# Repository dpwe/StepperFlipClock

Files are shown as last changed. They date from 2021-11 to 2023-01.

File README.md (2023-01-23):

# StepperFlipClock
2021-11-23

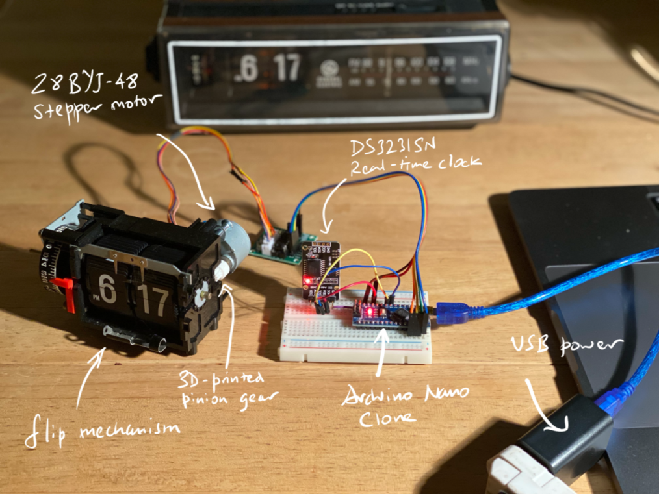
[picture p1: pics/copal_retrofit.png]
Copal retrofit components


Design and firmware for a stepper motor retrofit to the often-failed AC synchronous flip clock motors.

Flip clocks, perhaps most iconic from the repeating opening sequence of the movie Groundhog Day, are delightful mechanisms for rendering the time as digits by flipping through a set of leaves on a rotating drum like a rolodex.

They were popular as a "modern" clock in the 1960s and 70s, based on part on high-performance, mass-produced mechanisms from the Copal corporation in Japan, which manufactured high-quality flip mechanisms integrated with AC-synchronous motors, able to keep very accurate time thanks to the provision of extremely stable 50/60 Hz AC power by electrical utilities in many parts of the world.

Flip clocks were supplanted by the even more modern 7 segment LED clocks, and quartz time references, in the 1970s and 80s, but they now have a retro appeal. Unfortunately, the synchronous AC motors, spinning valiantly 8 times a second for 50 years or more, have long exceeded their design life and are mostly no longer functional.  They are no longer manufactured and no significant replacement stock has turned up.

At the same time, cheap and precise stepper motors of similar size and shape *are* available.  However, these need an entirely different source of time reference, and indeed require a microcontroller to operate.

This repo provides the resources for my investigations into stepper motor retrofit replacements for the original Copal synchronous motors found in the flip clocks made by GE (and Copal) in the eary 1970s.  I include the electronics design, the firmware (as Arduino sketches), and some pictures of a couple of finished clock conversions.

# BurstClockSerial

This version of the firmware winds on the flip mechanism in "bursts", once per minute.  This makes sure the flaps fall within a fraction of a second of the actual minute change; a regular flip mechanism typically has a variation of +/- 10 sec or more for any particular minute due to mechanical variations in the flaps.

The code has settings for two variations of the Copal mechanism, one with 60 teeth per hour on the main wheel (as found in GE clock-radios such as the 7-4305), and one with 50 teeth per hour (as in the Copal 227 alarm clock).

# synchronizer_nano

This sketch can be run on the same Arduino Nano that is driving the clock, but allows you to synchronize the DS3231 RTC chip to a time reference from a GPS.  You do this once, setting both the time and trimming the DS3231 to the GPS 1 second period, then you can re-run the BurstClockSerial to drive the clock.  To sync to GPS, you have to connect the GPS 1PPS signal to D2, and the GPS NMEA output to D8.

# StepperClockCopal.fzz

This is the Fritzing source for the hardware setup for the stepper clock.  It's mainly the wiring diagram that I've tried to make legible, although the schematic should be correct also.  It shows which Arduino pins are connected to which pins on the DS3231 RTC board, on the ULN2003A stepper driver board, as well as other hardware including the frontlight LED, the piezo buzzer, and the alarm microswitch.

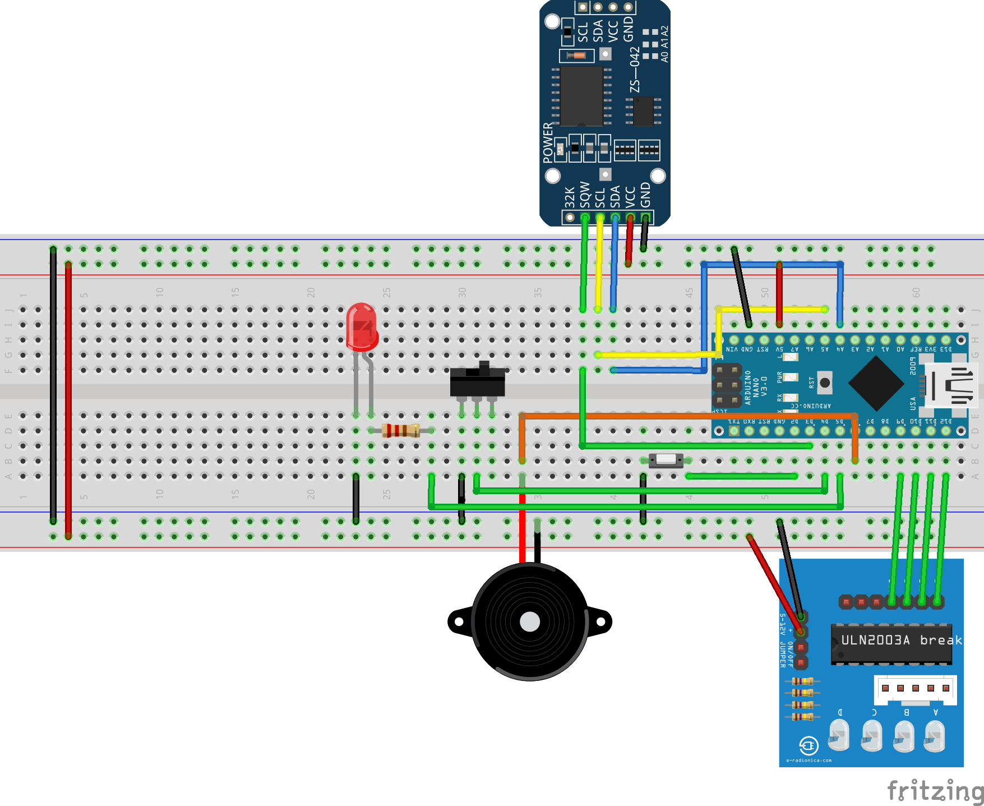
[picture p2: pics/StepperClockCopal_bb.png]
Stepper FlipClock Breadboard Layout


# 3Dprint

Directory containing the STL files I used for 3D printing pinion gears to mate the stepper motors with the flip clock mechanism.  `copol_pinion_1` works for the plastic-framed Copal mechanims.  `copol_pinion_2` attempted to scale down the teeth for the older, metal-framed mechanisms, but was a bit beyond the scale capabilities of the printing technology.  `copol_pinion_4b` converts the 5mm stepper shaft to the 2mm shaft on the original Copal motors, so you can take the small final gear off the early Copal motors and mount it on this 3D printed adapter.

# Gallery

In addition to the GE 7-4305 illustrated at the top of this page, I've also performed this retrofit on a Copal 227 which has much less space inside.  For this job, the power cord is replaced by a USB cord that plugs into an external USB power adapter at the mains plug.

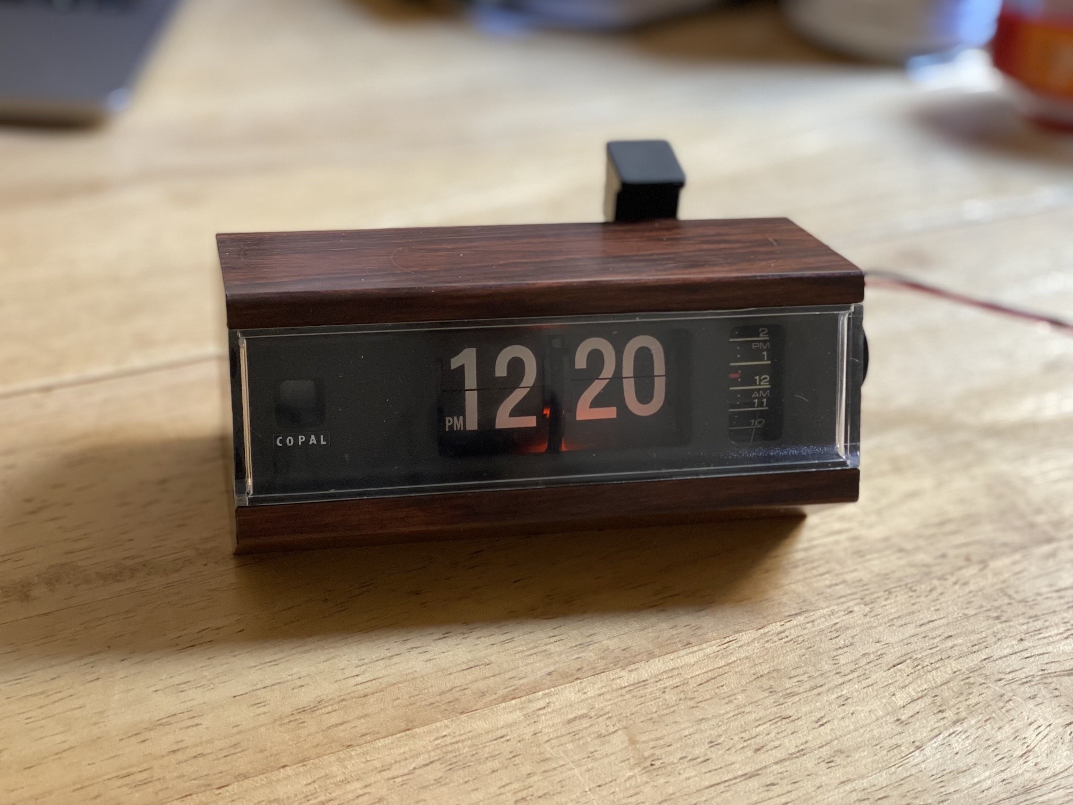
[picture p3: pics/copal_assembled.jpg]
Copal - assembled
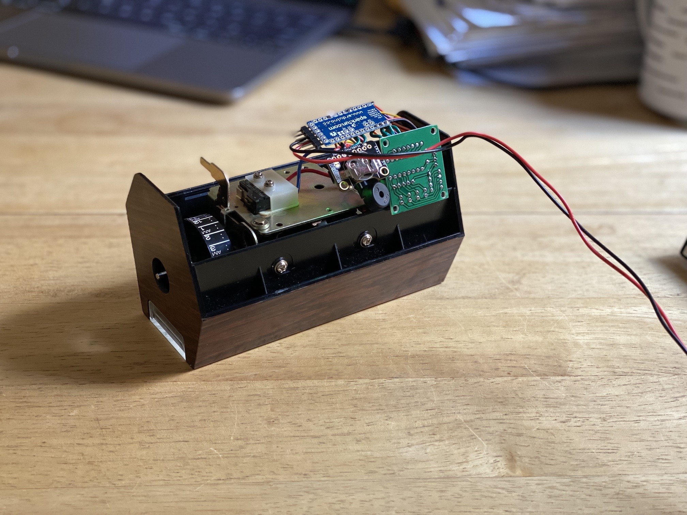
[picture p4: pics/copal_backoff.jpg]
Copal - back off
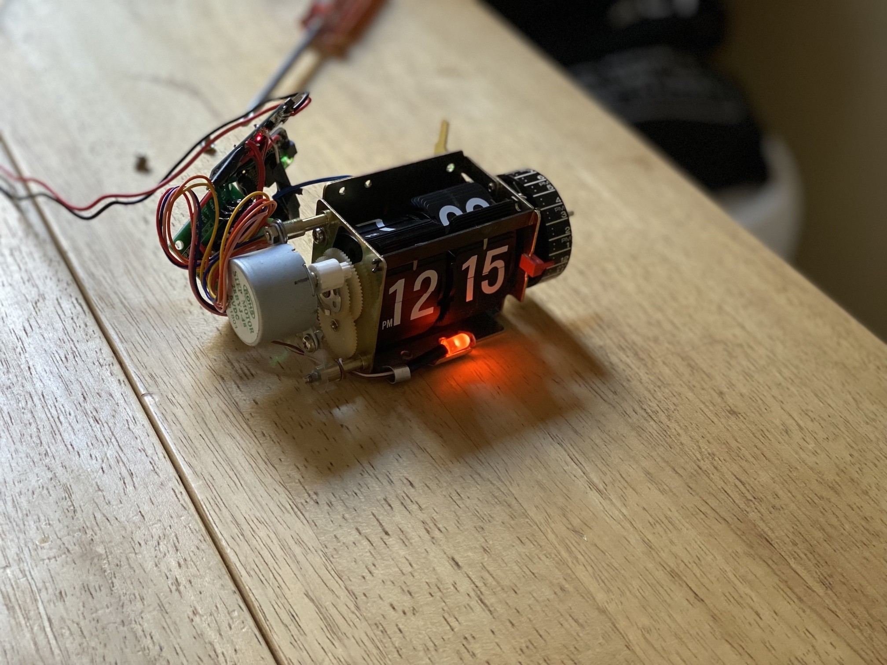
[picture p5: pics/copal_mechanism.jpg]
Copal - mechanism
  

# More Clock Adventures

See my [Clock Blog](https://dpwe.github.io/arduinoclocks/)

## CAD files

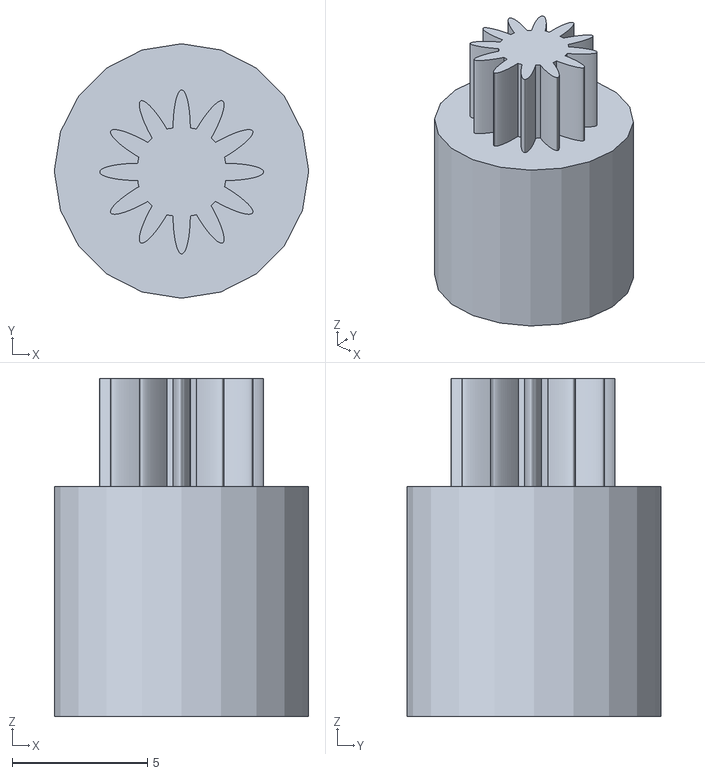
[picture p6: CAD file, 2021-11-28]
3Dprinting/copol_pinion_2.stl
9.40 x 9.40 x 12.5

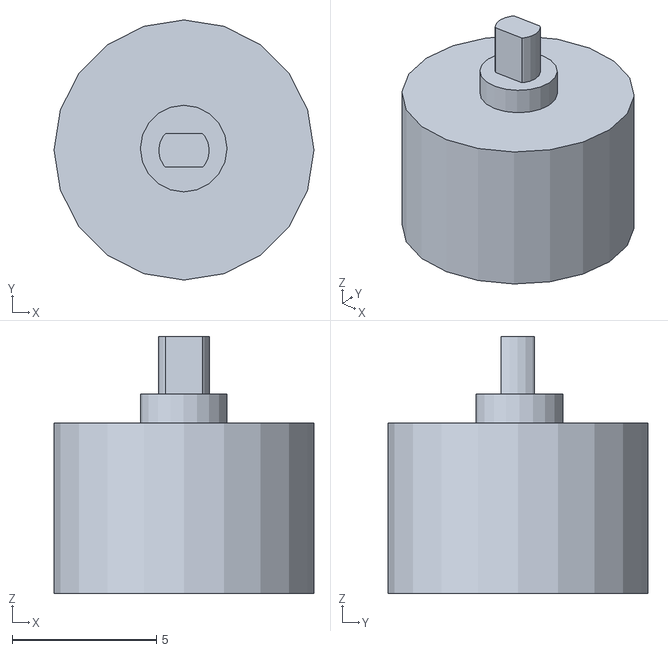
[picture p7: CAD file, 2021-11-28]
3Dprinting/copol_pinion_4b.stl
9.00 x 9.00 x 8.90

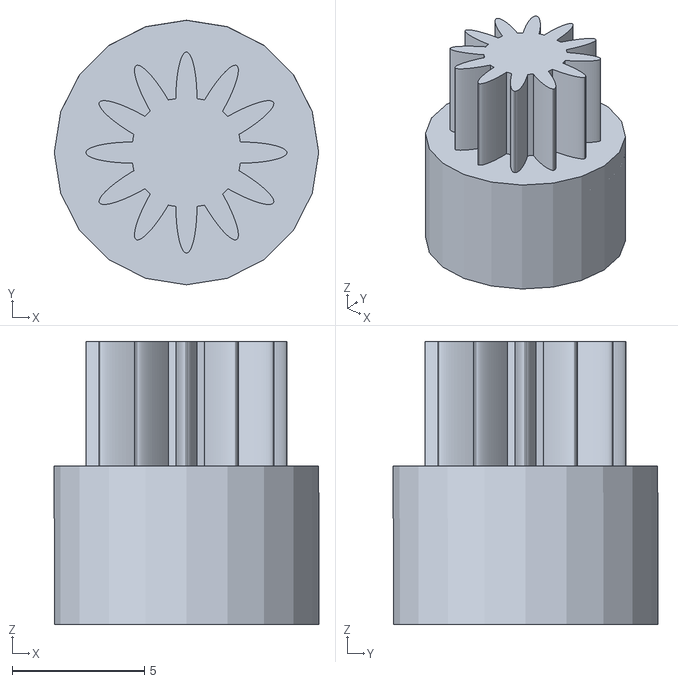
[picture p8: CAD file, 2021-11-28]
3Dprinting/copol_pinion_1.stl
10.0 x 10.0 x 10.7

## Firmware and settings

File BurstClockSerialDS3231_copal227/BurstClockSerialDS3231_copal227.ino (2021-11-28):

// BurstClockSerialDS3231.ino
// 
// Flip-clock-by-stepper-motor retrofit.
//
// Rather than emulating the continuous, slow rotation of the original Copal 60 Hz 
// synchronous motor, this version rotates by 1/12 rev as fast as possible once per
// minute.  This should allow us to control exactly when the flips fall, instead of 
// the +/- 15 sec of the original mechanism.  
//
// The code also aims to keep track of what the clock is currently displaying, and
// supports commanding to display arbitrary numbers.
//
// This version accepts control commands over the serial line.
// It uses the DS3231 instead of the MCP79412.  We use the DS3231's alarm register 
// as the battery-backed RAM to persist the current believed display state.

// Connections:
// ULN2003A board: (note, sequencing is backwards)
// IN1 -> D12
// IN2 -> D11
// IN3 -> D10
// IN4 -> D9
// DS3231 board:
// SDA -> A4
// SCL -> A5
// SQW -> D3 (supports interrupt)
// Clock Advance Button: -> D2 (pulls down to ground)
// Mechanical Alarm microswitch -> D4 (pulls down to ground when alarm should sound)
// Backlight LED -> D5 (supports Timer0 PWM, possibly interferes with delay() timer)
// Buzzer: Tone pattern on D6 (using Timer1, also D6 is OC0A, so might support PWM output)
// Time Wrong LED -> D13 (built-in LED)

// GE 7-4305
//#define STEPS_PER_CYCLE 2048
//#define MINUTES_PER_CYCLE 15
// Copal 227
#define STEPS_PER_CYCLE 1280
#define MINUTES_PER_CYCLE 9

#include <Tone.h>  // https://github.com/bhagman/Tone
Tone tone_out[2];  // Allocate two timers so we can *not* use tone_out[0],
                   // which tries to use Timer2 (but we have other plans).

#include <TimeLib.h>        // https://www.pjrc.com/teensy/td_libs_DS1307RTC.html
#include <Wire.h>           // https://www.arduino.cc/en/Reference/Wire

#include <Timezone.h>       // https://github.com/JChristensen/Timezone
// US Eastern Time Zone (New York, Detroit)
//TimeChangeRule myDST = {"EDT", Second, Sun, Mar, 2, -240};    //Daylight time = UTC - 4 hours
//TimeChangeRule mySTD = {"EST", First, Sun, Nov, 2, -300};     //Standard time = UTC - 5 hours
// US Pacific Time Zone (Las Vegas, Los Angeles)
TimeChangeRule myDST = {"PDT", Second, Sun, Mar, 2, -420};
TimeChangeRule mySTD = {"PST", First, Sun, Nov, 2, -480};
Timezone myTZ(myDST, mySTD);

#include <DS3231.h>         // https://github.com/NorthernWidget/DS3231
DS3231 ds3231;
RTClib RTC;

// -------------------------------------------------------------------
// Timer 2:
// Each time the stepper is advanced, Timer2 is set to generate an interrupt
// 3 ms later.  This interrupt either advances to the next step (if there are
// remaining steps to do) or powers down the coils.

// What to call on interrupt.
void (*_timeout_callback)(void);

// Timer2 Overflow Interrupt Vector
ISR(TIMER2_OVF_vect) {
  TIFR2 = 0x00;         // Timer2 INT Flag Reg: Clear Timer Overflow Interrupt
  TCCR2B = 0x00;        // Stop Timer2 until next timeout_restart().
  (*_timeout_callback)();
}

void timeout_setup(void (*callback_func)(void)) {
  // Set up Timer2 for the post-step timeout.
  TCCR2B = 0x00;        // Disable Timer2 while we set it up
  _timeout_callback = callback_func;
  TIFR2  = 0x00;        // Timer2 INT Flag Reg: Clear Timer Overflow Flag
  TIMSK2 = 0x01;        // Timer2 INT Reg: Timer2 Overflow Interrupt Enable
  TCCR2A = 0x00;        // Timer2 Control Reg A: Wave Gen Mode norm
}

void timeout_restart(unsigned int ms) {
  // Reset timeout timer (timer2). It counts up to 255 at 16 kHz, so 0 gives ~16ms, 128 is 8ms, 192 is 4ms.
  int init_val = 255 - (ms * 16);
  if (init_val < 0)  init_val = 0;  // max delay is 16 ms.
  TCNT2 = init_val;
  TCCR2B = 0x07;        // Timer2 Control Reg B: Timer Prescaler set to 1024 (starts the clock).
}

// -------------------------------------------------------------------
// Stepper motor control

// Pins to drive motor coils.
#define PIN_A 12
#define PIN_B 11
#define PIN_C 10
#define PIN_D 9

void stepper_setup(void)
{
  pinMode(PIN_A, OUTPUT);
  pinMode(PIN_B, OUTPUT);
  pinMode(PIN_C, OUTPUT);
  pinMode(PIN_D, OUTPUT);

  timeout_setup(next_step_callback);
}

void set_pins(int a, int b, int c, int d) {
  digitalWrite(PIN_A, a);
  digitalWrite(PIN_B, b);
  digitalWrite(PIN_C, c);
  digitalWrite(PIN_D, d);
}

void step_to_state(int state) {
  switch (state % 4) {
    // The "backwards" motion of the motor is encoded directly here.
    case 0:
      set_pins(0, 0, 1, 1);
      break;
    case 1:
      set_pins(0, 1, 1, 0);
      break;
    case 2:
      set_pins(1, 1, 0, 0);
      break;
    case 3:
      set_pins(1, 0, 0, 1);
      break;
  }
}

// Current steps within cycle of stepper
int _stepper_state = 0;
// We can peek at steps_to_do as a more informative alternative to stepper_active.
volatile long steps_to_do = 0;
// Semaphore that client writes to request more steps.  Gets cleared when accepted.
volatile long steps_to_do_semaphore = 0;
// Status that can be inspected by client.
volatile bool stepper_active = 0;

// When active, we advance the stepper every 3 ms.
#define MS_BETWEEN_STEPS 3

void next_step_callback(void)
{
  // This is usually executed in interrupt state, so be careful not to change variables used
  // outside, except the steps_to_do semaphore.
  if (steps_to_do_semaphore) {
    steps_to_do += steps_to_do_semaphore;
    steps_to_do_semaphore = 0;
  }
  if (steps_to_do) {
    stepper_active = 1;
    timeout_restart(MS_BETWEEN_STEPS);
    _stepper_state = (_stepper_state + 1) % STEPS_PER_CYCLE;
    step_to_state(_stepper_state);
    --steps_to_do;
  } else {
    // We are idling the stepper.
    stepper_active = 0;
    set_pins(0, 0, 0, 0);
    // Notify clients.
    //inc_display_minute();
    // Somehow this was being called during initialization and adding an extra minute.
    // Now inc_display_minute() is called by flip_update when it notices stepper_active 
    // has gone low.
  }
}

// Called by client to start new steps.
void add_steps(int steps) {
  // Drop the value into the semaphore; it will be added on to the total by the interrupt routine.
  Serial.print("add_steps=");
  Serial.println(steps);
  steps_to_do_semaphore = steps;
  if (!stepper_active) {
    // Calling next_step_callback will accept the semaphore, take a step immediately, then restart timer.
    next_step_callback();
  }
}

// ==========  persistent read/write =============

void save_display_state_to_sram(int mins_state) {
  // Write hrs/mins to DS3231 Alarm 2.  See DS3231.h
  byte disp_hour = (byte)(mins_state / 60);
  byte disp_min = (byte)(mins_state % 60);
  byte A2Day = 1, AlarmBits = 0;  // AlarmBits=0 means alarm when all of min, hr, day, month match.
  bool A2Dy = 0, A2h12 = 0, A2PM = 0;
  ds3231.setA2Time(A2Day, disp_hour, disp_min, AlarmBits, A2Dy, A2h12, A2PM);
}

int load_display_state_from_sram(void) {
  byte disp_hour, disp_min, A2Day, AlarmBits;
  bool A2Dy, A2h12, A2PM;
  ds3231.getA2Time(A2Day, disp_hour, disp_min, AlarmBits, A2Dy, A2h12, A2PM);
  if (A2h12 != 0) {
    Serial.println("DS3231 Alarm is in 12h mode - uh-oh!");
  }
  return 60 * (int)disp_hour + (int)disp_min;  
}

// -------------------------------------------------------------------
// Core flip-dispay driver.

// Keep track of where we are within the MINUTES_PER_CYCLE.
int current_minute = 0;
// Keep track of where we are within the STEPS_PER_CYCLE.
unsigned int current_step = 0;

#define MINS_PER_DAY 1440
// Believed current state of display, in minutes since midnight
// 0 = 00:00, 1439 = 23:59, -1 = unknown.
volatile int display_mins_shown = -1;

void inc_display_minute(void) {
  // Intended to be called by stepper interrupt routine when stepper goes idle because 
  // it has completed stepping.  However, it was being called "extra" during setup for 
  // an unexplained reason, so now it's called by the flip_update poll when it notices
  // a stepper command has finished.
  display_mins_shown = (display_mins_shown + 1) % MINS_PER_DAY;
}

void advance_one_minute(void) {
  ++current_minute;
  // Integer arithmetic - will round down.
  unsigned int new_step = (((long)current_minute * STEPS_PER_CYCLE) / MINUTES_PER_CYCLE);
  // Command the new steps to happen.
  add_steps(new_step - current_step);
  //Serial.print("steps: ");
  //Serial.println(new_step - current_step);
  // Update state.
  current_minute = current_minute % MINUTES_PER_CYCLE;
  current_step = new_step % STEPS_PER_CYCLE;
}

#define TIME_WRONG_LED LED_BUILTIN

void flip_setup(int initial_display_mins) {
  display_mins_shown = initial_display_mins;
  Serial.print("Setup ");
  flip_report_display(display_mins_shown);

  stepper_setup();
  // We use TIME_WRONG_LED to indicate when clock is "waiting" to catch up.
  pinMode(TIME_WRONG_LED, OUTPUT);
}

void set_time_error_led(bool state) {
  if (state) {
    digitalWrite(TIME_WRONG_LED, HIGH);
  } else {
    digitalWrite(TIME_WRONG_LED, LOW);    
  }
}

void printDigits(int digits)
{
  // utility function for digital clock display: prints preceding colon and leading 0
  if(digits < 10)
    Serial.print('0');
  Serial.print(digits);
}

// The time that we are trying to drive the display towards.
// -1 is a special value meaning don't update.
// Otherwise a value 0.1439 corresponding to 00:00 to 23:59.
int requested_time = -1;

void flip_report_display(int mins) {
  // Echo current belief about display.
  Serial.print("Display: ");
  printDigits(mins / 60);
  Serial.print(":");
  printDigits(mins % 60);
  // Also let us know what we're aiming for.
  Serial.print(" / Goal: ");
  printDigits(requested_time / 60);
  Serial.print(":");
  printDigits(requested_time % 60);  
  Serial.println();
}

void flip_set_state_mins(int mins) {
  // Somehow we got info about what the display currently says, during init.
  // Ignore -1
  if (mins < 0)
    return;
  display_mins_shown = mins;
  Serial.print("Warp ");
  flip_report_display(display_mins_shown);
  // Save display state in persistent RAM.
  save_display_state_to_sram(display_mins_shown);
}

// Time changes of up to two hours backwards will result in the 
// clock stopping until "real time" catches up.
#define MAX_PAUSE 120

bool minute_in_progress = false;

void flip_update(void) 
{
  // Called periodically in update loop.  Checks to see if we have stuff to do.
  if (stepper_active) {
    // An update is not yet complete.
    return;
  }
  if (minute_in_progress) {
      // We were advancing one minute, but now that's done.
      minute_in_progress = false;
      // Increment the minutes count (not done by stepper handler at present).
      inc_display_minute();
      flip_report_display(display_mins_shown);
      // Save display state in persistent RAM.
      save_display_state_to_sram(display_mins_shown);
  }
  // If requested_time is -1, don't do anything.
  if (requested_time >= 0 && (display_mins_shown != requested_time)) {
    set_time_error_led(true);
    // Maybe *don't* move the clock if the requested time is close to catching up.
    if ( ((requested_time - display_mins_shown + MINS_PER_DAY) % MINS_PER_DAY) 
         < (MINS_PER_DAY - MAX_PAUSE)) {
      // When we advance, we advance one minute at a time.
      minute_in_progress = 1;
      advance_one_minute();
    }
  } else {
    // We good.
    set_time_error_led(false);
  }
}

int move_to_time(int new_mins)
{
  requested_time = new_mins;
}

// -------------------------------------------------------------------
// Input commands over serial line

void cmd_setup(void) {
  // Nothing to do?
}

byte atoi2(char *s) {
  // Convert two ascii digits to a uint8.
  return (s[1] - '0') + 10 * (s[0] - '0');
}

int parse_string_to_mins(char *mins_string) {
  // Convert a string like "2359" into minutes since midnight (1439 in this case)
  if (strlen(mins_string) != 4) {
    Serial.println("Error: cmd arg string is not 4 chrs.");
    return -1;
  }
  int hours = atoi2(mins_string);
  int minutes = atoi2(mins_string + 2);
  return 60 * hours + minutes;
}

tmElements_t parse_time_string(char *time_string) {
  // time_string must point to exactly 14 chars in format YYYYMMDDHHMMSS.
  tmElements_t tm;
  if (time_string[0] != '2' or time_string[1] != '0') {
    Serial.println("Warn: Year does not start with 20...");
  }
  tm.Year = y2kYearToTm(atoi2(time_string + 2));
  tm.Month = atoi2(time_string + 4);
  tm.Day = atoi2(time_string + 6);
  tm.Hour = atoi2(time_string + 8);
  tm.Minute = atoi2(time_string + 10);
  tm.Second = atoi2(time_string + 12);
  return tm;
}

#define CMD_BUF_LEN 32
char cmd_buffer[CMD_BUF_LEN];
int cmd_len = 0;

bool enable_rtc_updates = true;

byte backlight_led = 5;
byte backlight_brightness = 64;

void cmd_update(void) {
  if (Serial.available() > 0) {
    // read the incoming byte:
    char new_char = Serial.read();
    if (new_char == '\n') {
      // handle command.
      cmd_buffer[cmd_len] = '\0';
      if (cmd_len > 0) {
        byte cmd0 = cmd_buffer[0];
        if (cmd0 >= 'a')  cmd0 -= ('a' - 'A');
        switch (cmd0) {
          case 'D':
            // Specify display request: D2359
            // Any invalid time string (eg. D-1) will stop the system trying to reach the time.
            move_to_time(parse_string_to_mins(cmd_buffer + 1));
            break;
          case 'W':
            // Warp display state (to match actual display): W2359
            flip_set_state_mins(parse_string_to_mins(cmd_buffer + 1));
            break;
          case 'T':
            // Enable (T1) / disable (T0) RTC time updates, or toggle: T
            enable_rtc_updates = (cmd_len==1) ? !enable_rtc_updates : (cmd_buffer[1] == '1');
            Serial.print("enable_rtc_updates: ");
            Serial.println(enable_rtc_updates);
            break;
          case 'S':
            // Execute some individual steps, bypassing the flip manager.
            // Typically, one minute is 170 or 171 steps (142 for Copal227).
            // We can use this to trim the stepper to be "mid cycle": 
            //  - slowly wind on by ~10 steps until flap falls
            //  - step on 85 (71) steps to be mid-cycle
            //  - Warp display to current reading, you are now good.
            add_steps(atoi(cmd_buffer + 1));
            break;
          case 'B':
            // Set backlight brightness 0..255.
            backlight_brightness = atoi(cmd_buffer + 1);
            analogWrite(backlight_led, backlight_brightness);
            break;
          case 'Z':
            // Set date/time: Z20211118094000 - 2021-11-18 09:40:00.
            if (strlen(cmd_buffer) != 15) {
              Serial.println("Bad format - Zyyyymmddhhmmss");
            } else {
              RTC_set_time(parse_time_string(cmd_buffer + 1));
            }
            break;
        }
      }
      cmd_len = 0;
    } else {
      if (cmd_len < CMD_BUF_LEN) {
        cmd_buffer[cmd_len++] = new_char;
      }
    }
  }
}

// -------------------------------------------------------------------
// Pin3 interrupt service
const byte INTERRUPT_PIN = 3;
volatile long tick_micros = 0;

void tick_ISR(void) {
  // Record the micros when tick occurs.
  tick_micros = micros();
}

void int_setup(void) {
  // Set interrupt input pin
  pinMode(INTERRUPT_PIN, INPUT_PULLUP);
  // Attach the tick ISR
  attachInterrupt(digitalPinToInterrupt(INTERRUPT_PIN), tick_ISR, FALLING);
}

long last_tick_micros = 0;

void int_update(void) {
  // Did the ISR update tick_micros?
  if (tick_micros != last_tick_micros) {
    Serial.print("Micros since last tick=");
    Serial.println(tick_micros - last_tick_micros);
    // Clear the interrupt.
    ds3231.checkIfAlarm(1);
    // Make sure the alarm is on.
    ds3231.turnOnAlarm(1);
    last_tick_micros = tick_micros;
  }
}

// -------------------------------------------------------------------
// Real-time clock.

//const int tz_offset = -4;  // Eastern Daylight Time (USA)

//time_t RTC_tzlocal_get(void) {
//  time_t utc_time = RTC.now().unixtime();
//  time_t local_time = utc_time + tz_offset * SECS_PER_HOUR;
//  return local_time;
//}

time_t RTC_utc_get(void) {
  return RTC.now().unixtime();
}

time_t now_local(void) {
  // Like now(), but includes timezone modification.
  return myTZ.toLocal(now());
}

void RTC_setup(void) {
  // Have the now() function return UTC.
  setSyncProvider(RTC_utc_get);   // the function to get the time from the RTC
  if(timeStatus() != timeSet)
     Serial.println("Unable to sync with the RTC");
  else {
     Serial.println("RTC has set the system time");
     tmElements_t tm;
     breakTime(now_local(), tm);
     serial_print_tm(tm);
  }
  // Set up the SQWV output. 0 = 1 Hz, 1 = 1024 Hz, 2 = 4096 Hz, 8 = 8192 Hz.
  byte frequency = 0;
  ds3231.enableOscillator(true, /* battery= */ false, frequency);
  // Actually, let's have Alarm1 interrupt us every minute.  AlarmBits is value from 
  // p12 table2 of https://datasheets.maximintegrated.com/en/ds/DS3231.pdf
  // (I guess AlarmBits 0..3 are used for Alarm1 control, in setA1Time().)
  // 0xF = every second, 0xE = when seconds match; 0xC = min & sec match; 
  // 0x8 = hour, min, sec match; 0x0 = day/date, hour, min, sec match.
  ds3231.setA1Time(/* Day */ 0, /* Hour */ 0, /* Minute */ 0, /* Second */ 0,
                   /* AlarmBits= */ 0x0E, false, false, false);
  // Clear the interrupt.
  ds3231.checkIfAlarm(1);
  // Set SQWV output to Alarm interrupts, and enable Alarm1.
  ds3231.turnOnAlarm(1);
}

void RTC_set_time(const tmElements_t& tm) {
  // Set the DS3231 time.
  Serial.print("Set RTC: ");
  serial_print_tm(tm);
  ds3231.setYear(tmYearToY2k(tm.Year));
  ds3231.setMonth(tm.Month);
  ds3231.setDate(tm.Day);
  ds3231.setHour(tm.Hour);
  ds3231.setMinute(tm.Minute);
  ds3231.setSecond(tm.Second);
  // Resync TimeLib
  //setTime(tm.Hour, tm.Minute, tm.Second, tm.Day, tm.Month, tm.Year);
  setTime(RTC_utc_get());
}

int last_time_mins = -1;

void RTC_update(void) {
  // See if the minutes have changed.
  tmElements_t tm;
  breakTime(now_local(), tm);
  int time_mins = tm.Hour * 60 + tm.Minute;
  if (time_mins != last_time_mins) {
    Serial.print("Ard: ");
    serial_print_tm(tm);
    // Let's see how we're doing relative to the RTC.
    Serial.print("RTC: ");
    breakTime(RTC_utc_get(), tm);
    serial_print_tm(tm);    
    // Advance the flip display.
    if (enable_rtc_updates) {
      move_to_time(time_mins);
    }
    last_time_mins = time_mins;
  }
}

void serial_print_tm(const tmElements_t &tm)
{
  Serial.print(tmYearToCalendar(tm.Year));
  Serial.print("-");
  printDigits(tm.Month);
  Serial.print("-");
  printDigits(tm.Day);
  Serial.print(" ");
  printDigits(tm.Hour);
  Serial.print(":");
  printDigits(tm.Minute);
  Serial.print(":");
  printDigits(tm.Second);
  Serial.println();
}

// ------------------------
// Other misc system (tone generator, LEDs, wind-on button).

#define WIND_ON_BTN_PIN 2
#define BUZZER_PIN 6
#define ALARM_IN_PIN 4

void sys_setup(void) {
    tone_out[0].begin(2);  // This is a dummy, to stop Timer2 being used.
    tone_out[1].begin(BUZZER_PIN);  // This tone is assigned to Timer1, we'll use it.
    
    pinMode(backlight_led, OUTPUT);
    
    analogWrite(backlight_led, backlight_brightness);

    // Override tone_out[0] to use D2 as button input.
    pinMode(WIND_ON_BTN_PIN, INPUT_PULLUP);
    // Pulled down by the alarm microswitch.
    pinMode(ALARM_IN_PIN, INPUT_PULLUP);
}

int loop_count = 0;

void sys_update(void) {
  // Expect calls ~ every 10 ms.
  ++loop_count;
  if ((loop_count % 15) == 0) {
    // Once every 150 ms.
    if (loop_count <= 60) {
      // If the alarm switch is down, play a 50 ms 4kHz pip on the first 4 of 6 steps.
      if (digitalRead(ALARM_IN_PIN) == LOW) {
        tone_out[1].play(4000, 50);
      }
    }
  }
  loop_count %= 90;  // 90 x 10ms cycle

  // Check the wind-on button.
  byte button_down = 1 - digitalRead(WIND_ON_BTN_PIN);
  if (button_down) {
    // If button is down and stepper is about to stop stepping, add more steps.
    // We expect this to be updated every 10ms, so add if we have less than 10ms of steps left.
    if (steps_to_do < 5) {
      add_steps(10);
    }
  }
}

// ----------------------------------------------------------
// Arduino routines.

void setup() {
    // Start the I2C interface
    Wire.begin();

    // initialize serial communication at 9600 bits per second.
    Serial.begin(9600);
    
    Serial.println("Post-reset settling...");
    delay(2000);

    // Restore saved display state (from previous run or set_time_in_rtc_sram).
    long saved_display_time = load_display_state_from_sram();
    flip_setup(saved_display_time);
    RTC_setup();
    cmd_setup();
    int_setup();
    sys_setup();
}

void loop() {
  RTC_update();
  flip_update();
  cmd_update();
  int_update();
  sys_update();
  delay(10); // ~100 Hz looping.
}

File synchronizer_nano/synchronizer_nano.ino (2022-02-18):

// Synchronizer_nano
//
// Get time from RTC chip and GPS.
// Display relative time alignment of each (relative to millis())
// Allow synchronization to each
// Emit time sync messages over serial on demand.

// This version runs on an Arduino Nano without display, control/display via USB serial.

// Wiring:
// Arduino <> DS3231
//     GND -> GND
//     5V  -> VCC
//     A5  -> SCK
//     A4  -> SDA
//     D3  <- SQWV

// Arduino <> UGPSM
//     GND -> GND
//     5V  -> VCC
//     D8  <- TX   (for AltSoftSerial)
//     D2  <- 1PPS


#include <Wire.h>

#include <TimeLib.h>        // https://www.pjrc.com/teensy/td_libs_DS1307RTC.html

// =============================================================
// PPS change time recording.
// =============================================================

const int sqwPin = 3; // The number of the pin for monitor alarm status on DS3231
const int ppsPin = 2; // PPS output from GPS board

const int ledPin = 13; // On-board LED

volatile unsigned long rtc_micros = 0;
volatile unsigned long gps_micros = 0;

void rtc_mark_isr(void)
{
  rtc_micros = micros();
}
void gps_mark_isr(void)
{
  gps_micros = micros();
}

void setup_interrupts() {
  // DS3231 is on falling edge.
  attachInterrupt(digitalPinToInterrupt(sqwPin), rtc_mark_isr, FALLING);
  // GPS mark is on rising edge.
  attachInterrupt(digitalPinToInterrupt(ppsPin), gps_mark_isr, RISING);
} 

// ======================================================
// Base Clock class tracks unixtime rel to millis/micros.
// ======================================================

// Ignore the first few syncs for RTC and GPS, to avoid noisy initial pulses.
#define MIN_SYNC_COUNT 4
// How many secs back to let the oldest sync go.  
// We have one actual tick per 4 us, so 40 sec is 10,000,000 actual ticks.
#define OLDEST_CLOCK_SYNC_SECS 40

class Clock {
 public:
  const char *name_ = 0;
  // base_unixtime_ corresponds to base_micros_.
  time_t base_unixtime_ = 0;
  unsigned long base_micros_ = 0;
  bool synced_ = false;
  // Calibrated system ticks per Clock's second.  
  // This is stored in tenths of microseconds to allow fractional microseconds.
  long decimicros_per_sec_ = 10000000;   // 10^7
  // for time since oldest sync.
  time_t oldest_sync_unixtime_ = 0;
  unsigned long oldest_sync_micros_ = 0;
  // Store one intermediate value so we can hop.
  time_t next_oldest_sync_unixtime_ = 0;
  unsigned long next_oldest_sync_micros_ = 0;
  // Count how many syncs we've received.
  int sync_count_ = 0;
  int min_sync_count_ = 0;

  Clock(const char *name, int min_sync_count=MIN_SYNC_COUNT) 
    : name_(name), min_sync_count_(min_sync_count) {}

  long skew_micros(Clock& ref) {
    // Report the delay in *system micros* between ref clock reaching a time and this clock reaching the same time.
    // A positive skew means this clock is behind the ref clock.
    // This only compares the last sync times of each clock, not actual "current" time.
    // If this clock is slow relative to ref clock, skew_micros will increas with time.
    // Strictly, value depends on whether we're evaluating it at this.base_unixtime_, or ref.base_unixtime_.  
    // Use ref, because ref.micros_per_sec is less likely to be wildly off.
    long micros_per_sec = (ref.decimicros_per_sec_ + 5) / 10;  // Apply rounding.
    return (base_micros_ - ref.base_micros_) - micros_per_sec * (base_unixtime_ - ref.base_unixtime_);
  }

  long unixtime(void) {
    // Return current time in seconds + milliseconds.
    unsigned long micros_since_base = micros() - base_micros_;
    long seconds_since_base = (10 * micros_since_base) / decimicros_per_sec_;
    return base_unixtime_ + seconds_since_base;
  }

  void sync(time_t sync_unixtime, unsigned long sync_micros=0) {
    // Sync the clock to sync_unixtime exactly now (or at sync_micros).
    ++sync_count_;
    if (sync_micros == 0) {
      sync_micros = micros();
    }
    if (sync_count_ > min_sync_count_) {
      if (oldest_sync_micros_ == 0) {
        oldest_sync_micros_ = sync_micros;
        oldest_sync_unixtime_ = sync_unixtime;
        next_oldest_sync_micros_ = sync_micros;
        next_oldest_sync_unixtime_ = sync_unixtime;
      } else {
        if ((sync_unixtime - next_oldest_sync_unixtime_) > OLDEST_CLOCK_SYNC_SECS) {
          // Push a (time, micros) sync pair onto the (short) queue every 2 minutes.
          oldest_sync_micros_ = next_oldest_sync_micros_;
          oldest_sync_unixtime_ = next_oldest_sync_unixtime_;
          next_oldest_sync_micros_ = sync_micros;
          next_oldest_sync_unixtime_ = sync_unixtime;
        }
        // This is going to wrap at 2**32 / 1e7 = 420 secs, or about 7 minutes.
        // Hopefully the queue will ensure it's never more than ~4 minutes.
        int delta_seconds = sync_unixtime - oldest_sync_unixtime_;
        if (delta_seconds < 400) {
          decimicros_per_sec_ = (10 * (sync_micros - oldest_sync_micros_)) / 
                                delta_seconds;
        }
      }
    }
    base_micros_ = sync_micros;
    base_unixtime_ = sync_unixtime;
    synced_ = true;
  }

  void clear_sync_history(void) {
    // If we think there's a discontinuity in sync history.
    oldest_sync_unixtime_ = 0;
    oldest_sync_micros_ = 0;
    next_oldest_sync_unixtime_ = 0;
    next_oldest_sync_micros_ = 0;
    sync_count_ = 0;
    synced_ = false;
  }

};

Clock rtc_clock("RTC");
Clock gps_clock("GPS");
Clock *sys_clock = &rtc_clock;

// ======================================================
// Track RTC times.
// ======================================================

#include "RTClib.h"
RTC_DS3231 rtc;

// from DS3231.cpp
#define CLOCK_ADDRESS 0x68

void ds3231_readAllRegisters(byte *registers, int num_bytes /* =19 */) {
  // Read all 19 bytes from the clock status.
  if (num_bytes > 19) num_bytes = 19;
  Wire.beginTransmission(CLOCK_ADDRESS);
  Wire.write(0x0);
    Wire.endTransmission();
    Wire.requestFrom(CLOCK_ADDRESS, num_bytes);
  for(int i = 0; i < num_bytes; ++i) {
     registers[i] = Wire.read();
  }
}

int ds3231_getAgingOffset(void) {
  // Read aging offset register
  Wire.beginTransmission(CLOCK_ADDRESS);
  Wire.write(0x10);
  Wire.endTransmission();
  Wire.requestFrom(CLOCK_ADDRESS, 1);
  int regVal = Wire.read();
  if (regVal > 127) regVal -= 256;
  return regVal;
}

void ds3231_setAgingOffset(int offset) {
  // Write the aging register. 
  // It's a signed 8 bit value, -128..127
  // Crystal *slows* by approx 0.1 ppm per unit.
  Wire.beginTransmission(CLOCK_ADDRESS);
  Wire.write(0x10);
  Wire.write(offset);
  Wire.endTransmission();
}

bool pending_RTC_interrupt = false;

unsigned long last_rtc_micros = 0;

void sync_time_from_RTC(void) {
  // This is called soon after an A0 transition is detected, so RTC unixtime is still current.
  rtc_clock.sync(rtc.now().unixtime(), rtc_micros);
  last_rtc_micros = rtc_micros;
}
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

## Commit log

2021-11-24 Firmware as shipped on first Copal 227 prototype.
2021-11-24 Fritzing file for stepper motor Arduino circuit
    [StepperClockCopal.fzz]
2021-11-28 Added pinion gear STL files.
    [copol_pinion_1.stl, copol_pinion_2.stl, copol_pinion_4b.stl]
